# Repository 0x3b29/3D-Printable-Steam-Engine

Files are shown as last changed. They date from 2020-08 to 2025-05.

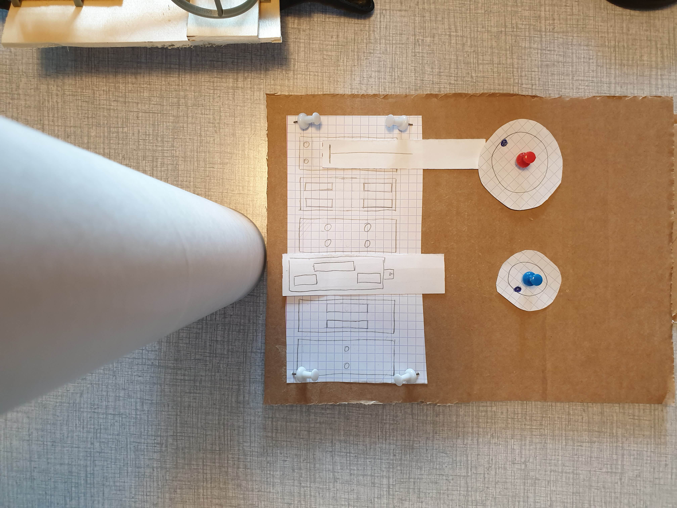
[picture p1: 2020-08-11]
Sketch/Step_2.jpg

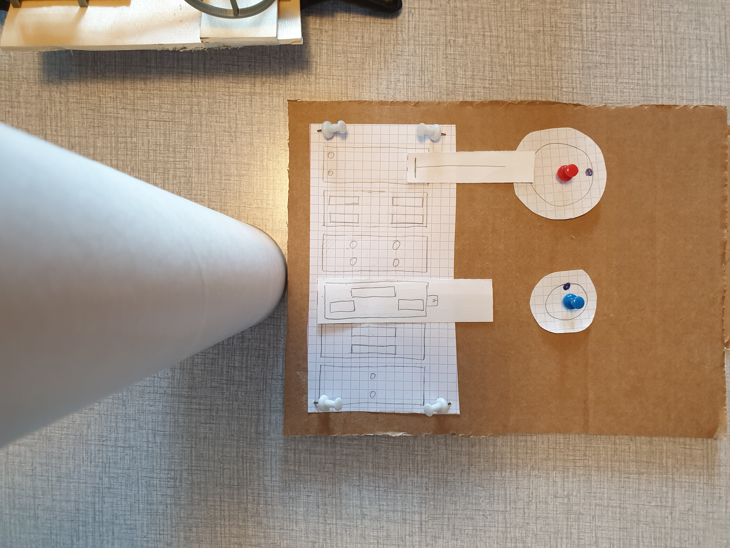
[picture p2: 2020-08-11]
Sketch/Step_5.jpg

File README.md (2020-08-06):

<h1>3D-Printable-Steam-Engine </h1>

<h2>Abstract</h2>

The goal of this project was to design a 3D printable steam engine. I challenged myself to come up with a design without looking up anything at all. I wanted to see how far I could get with only the knowledge I learned over time. To be honest, I did not expect getting very far, regardless getting a one and a four stroke variant to work.

<h2>Description</h2> 

This repository contains two variants of a design I came up in the spring 2020. It is inefficient and lacks the ability to work in both direktions. Also, there are quite some leeks which is an inherent flaw of 3D printing pressurized components whithout any seals. To get it to work, you need a source of pressurized gas. I used my dad's airbrush compressor. The air inlet in both designs is a replicaiton of the airbrush connection. This means you can connect a standard 2.5 mm hose to the 3D print. The 1 stroke design can operate with much lower pressure and spins at a higher rpm. The four stroke however is capable of starting in every position. The one stroke can stop at a dead point where you need to push it to get it spinning again. Also, since the leeks are four times higher in the four stroke engine, this variant uses much more air.

<h2>Printing</h2>
* All the parts can be printed in PLA (which I did). Since PLA is not very heat resilient, you should not try to power it with real steam tho
* Besides the crankshaft and the base, all other parts can be orientated in a way that they don't need supports
* All parts worked great printed with 0.2mm layer height
* To speed things up, the base plate and the stand can be printed whith 0.3mm layer height 

<h2>Assembly</h2>
* You need a 3mm drill to widen the holes in the lids. The pistons should slide smoothly through the cylinder and the lids. More clearance means less energy, so be conservative at first.
* You need a thin long strip op fine sanding paper to get the crankshafts smooth such that the connecting rods can move whithout a lot of resistance
* The Pistons need to be glued together. I used standard superglue for this. It is crucial that both piston halfs are very precisely glued to minimize friction
* You should break the corners of the slider(s) first to see if the sides need to be sanded down.
* To connect the piston rods with the pistons, I used small pieces of electrical copper wire.
* I did not need any oil to get both variants to work.

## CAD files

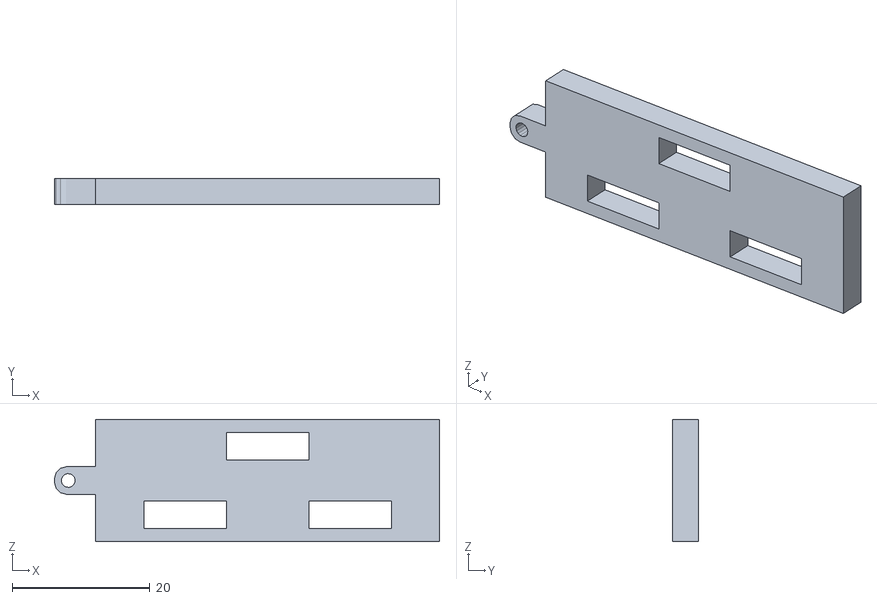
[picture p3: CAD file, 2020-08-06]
1 Stroke/Slider.stl
56.0 x 3.80 x 17.8

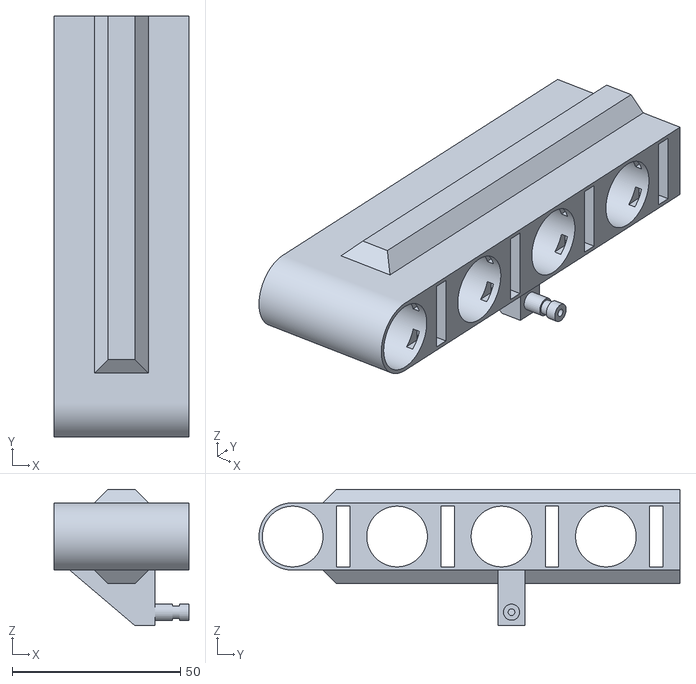
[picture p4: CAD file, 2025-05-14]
4 Stroke/Housing.stl
40.0 x 125.0 x 40.5

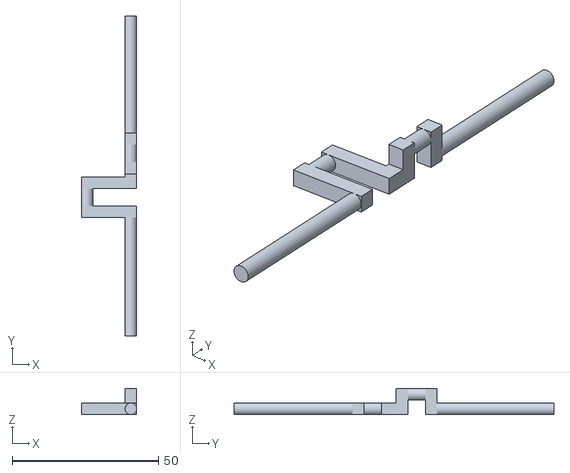
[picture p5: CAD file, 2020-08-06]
1 Stroke/Crank_Shaft.stl
19.0 x 109.5 x 9.00

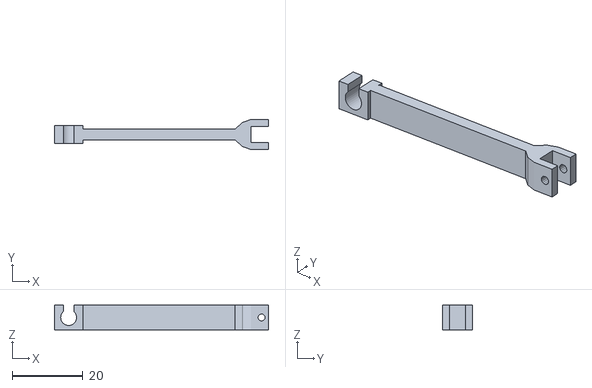
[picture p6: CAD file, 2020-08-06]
4 Stroke/Piston_Connecting_Rod.stl
60.5 x 8.50 x 7.00

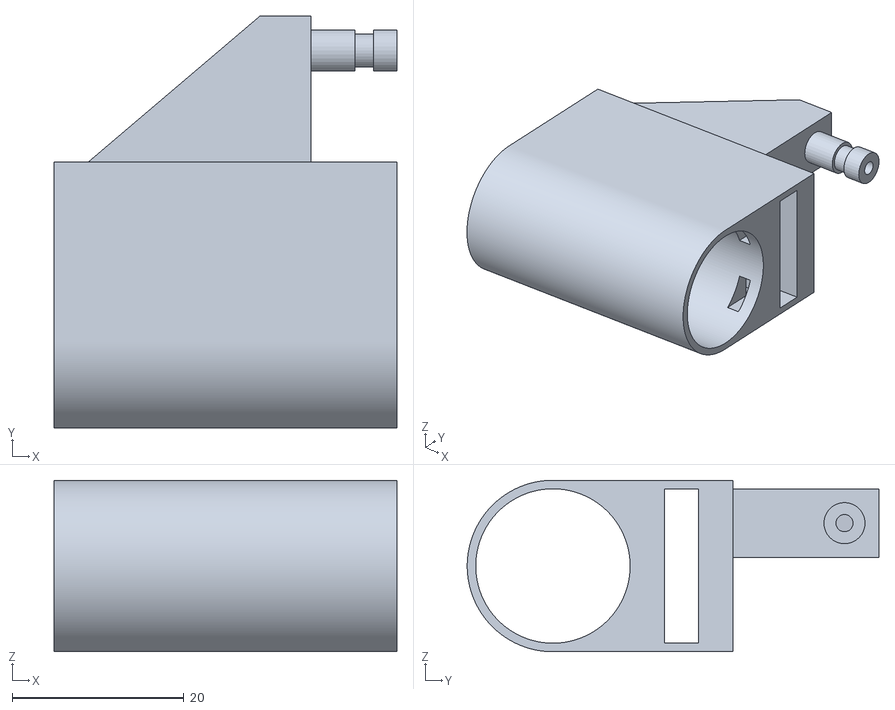
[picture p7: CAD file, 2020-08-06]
1 Stroke/Housing.stl
40.0 x 48.0 x 20.0

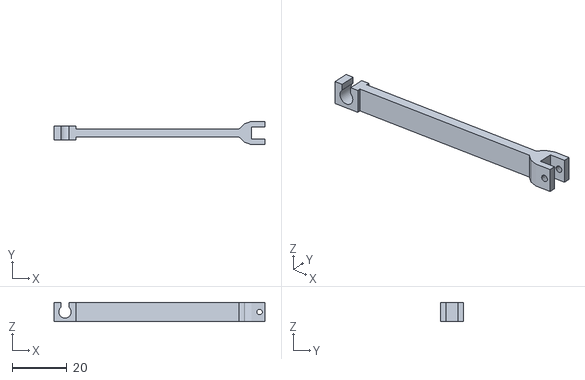
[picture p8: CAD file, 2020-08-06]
4 Stroke/Slider_Connecting_Rod.stl
77.0 x 8.50 x 7.01

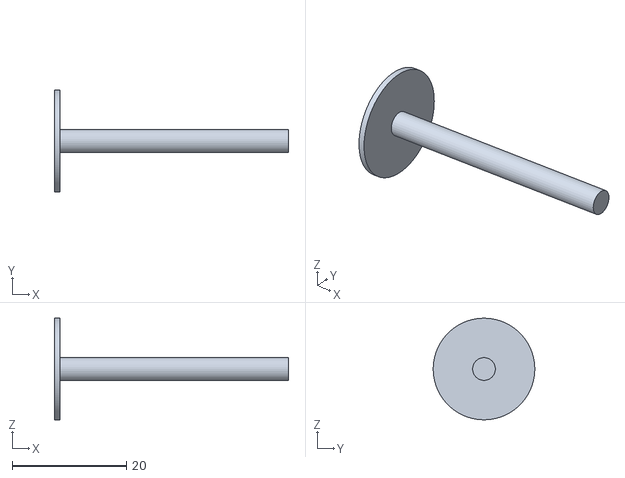
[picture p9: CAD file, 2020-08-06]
1 Stroke/Rear_Piston.stl
41.0 x 17.8 x 17.8

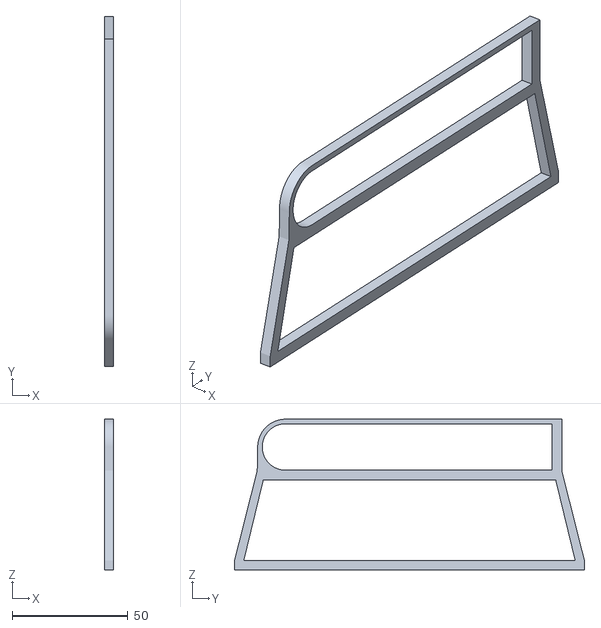
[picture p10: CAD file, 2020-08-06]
4 Stroke/Stand_Housing_Fixation_x2.stl
4.00 x 151.0 x 65.0

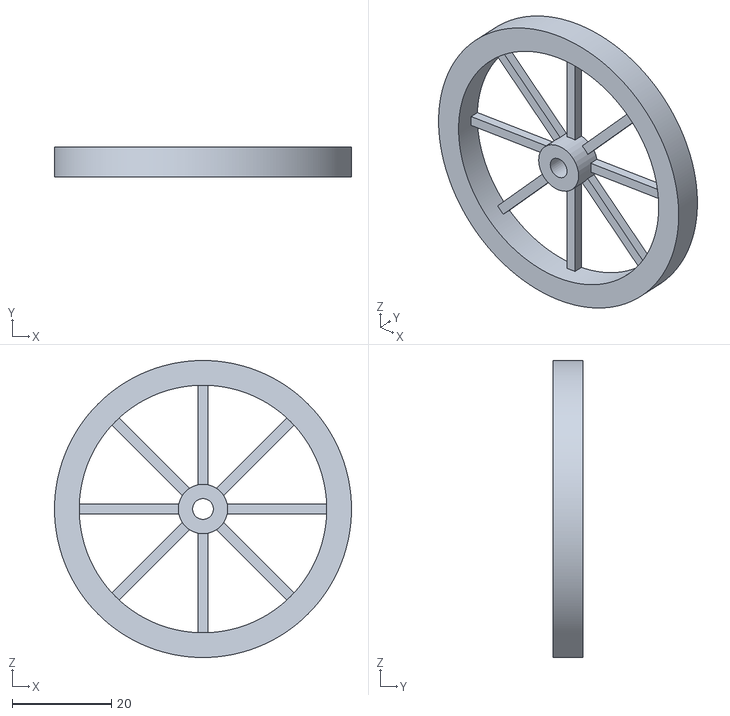
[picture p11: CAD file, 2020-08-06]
4 Stroke/Flywheel.stl
60.0 x 6.00 x 60.0

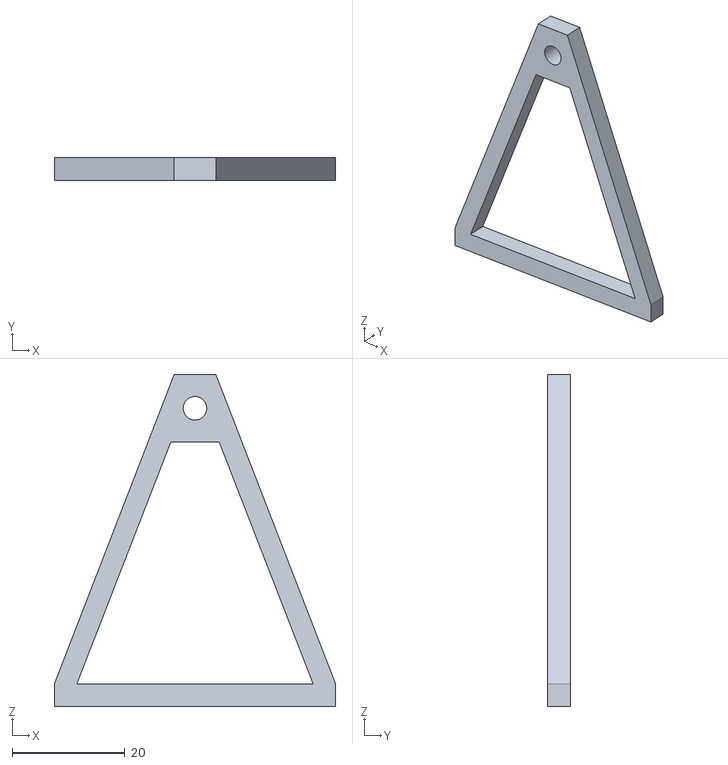
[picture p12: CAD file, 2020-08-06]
1 Stroke/Stand_Crankshaft_x2.stl
50.0 x 4.00 x 59.0

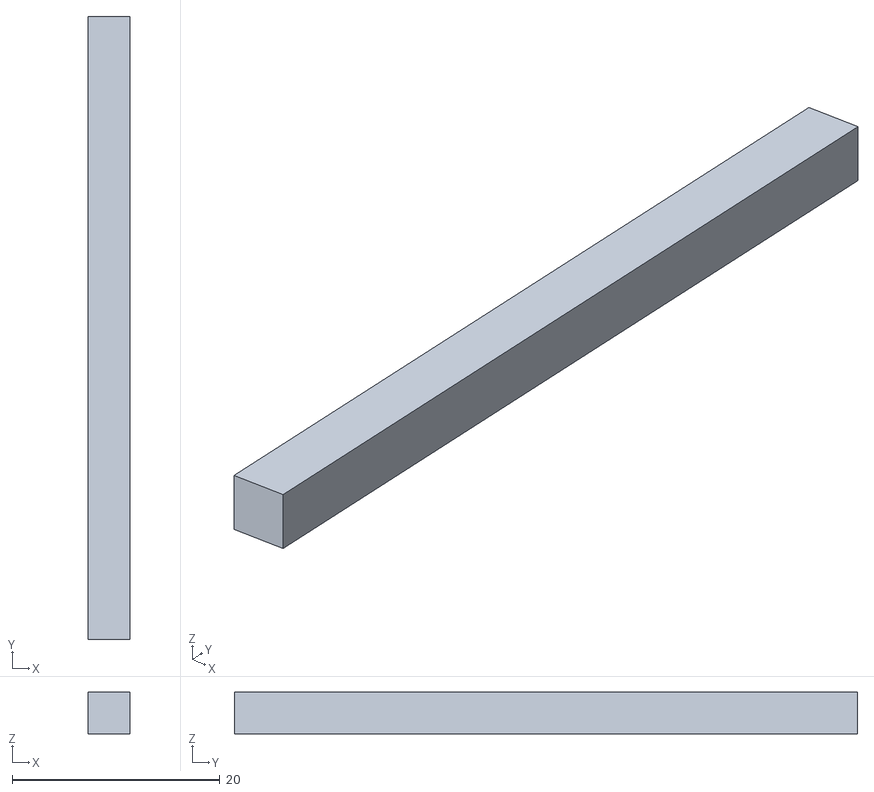
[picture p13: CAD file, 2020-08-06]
1 Stroke/Stand_Crankshaft_Fixation_x2.stl
4.00 x 60.0 x 4.00

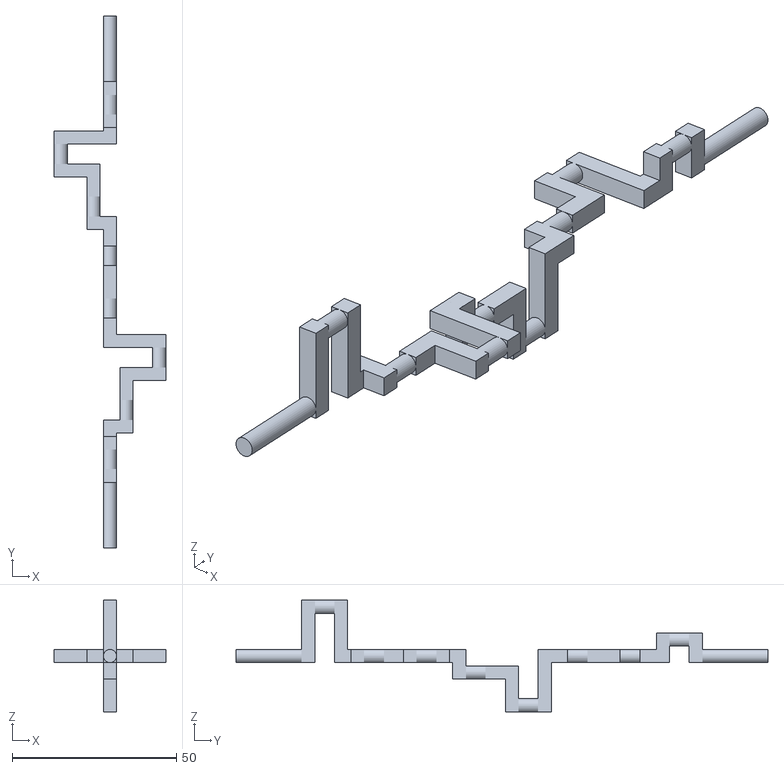
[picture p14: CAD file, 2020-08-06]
4 Stroke/Crankshaft.stl
34.0 x 162.0 x 34.0

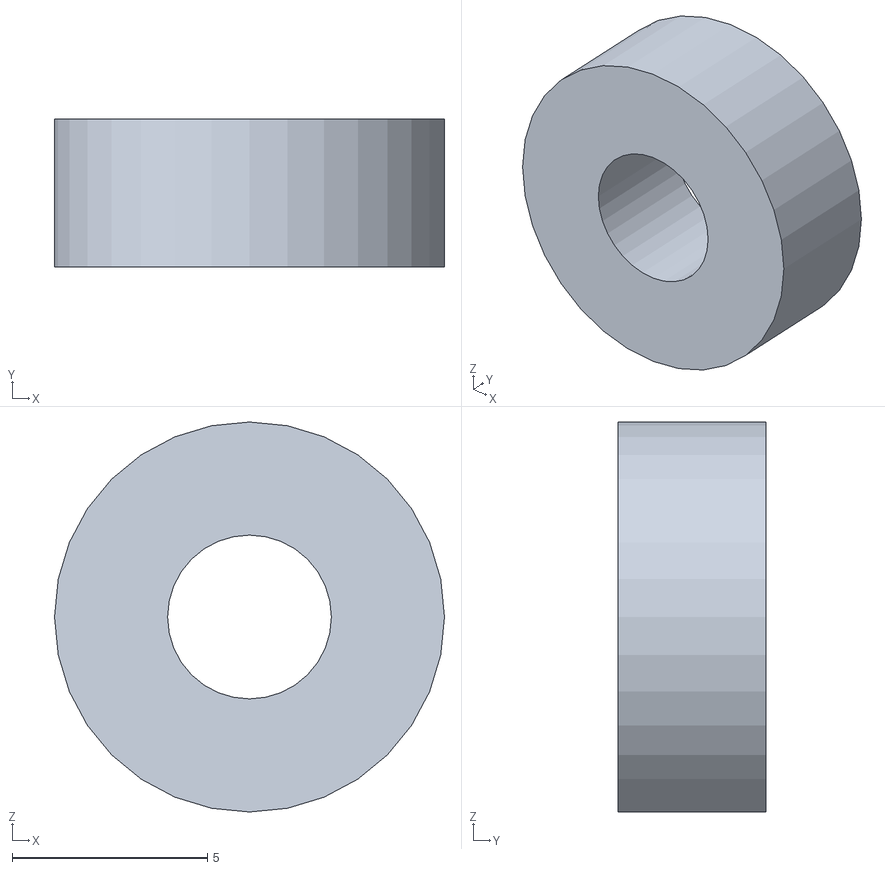
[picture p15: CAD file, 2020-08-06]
1 Stroke/Stopper_x2.stl
10.0 x 3.80 x 10.00

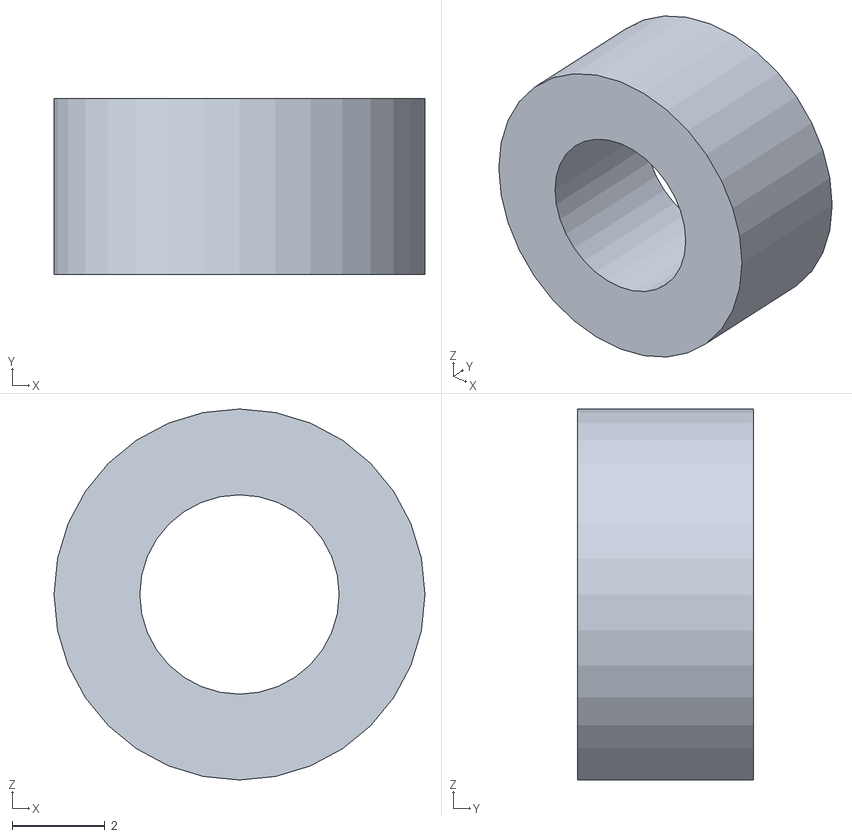
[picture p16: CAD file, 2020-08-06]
4 Stroke/Spacer_x4.stl
8.00 x 3.80 x 8.00

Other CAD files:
1 Stroke/Stand_Housing_Fixation_x2.stl
1 Stroke/Lid_x2.stl
1 Stroke/Piston_Front.stl
1 Stroke/Pulley.stl
1 Stroke/Stand.stl
1 Stroke/Stand_Housing_x2.stl
1 Stroke/steam_v1_0_1.blend
4 Stroke/Lid_x2.stl
4 Stroke/Piston_Front.stl
4 Stroke/Pulley.stl
4 Stroke/Stand.stl
4 Stroke/Stand_Housing_x2.stl

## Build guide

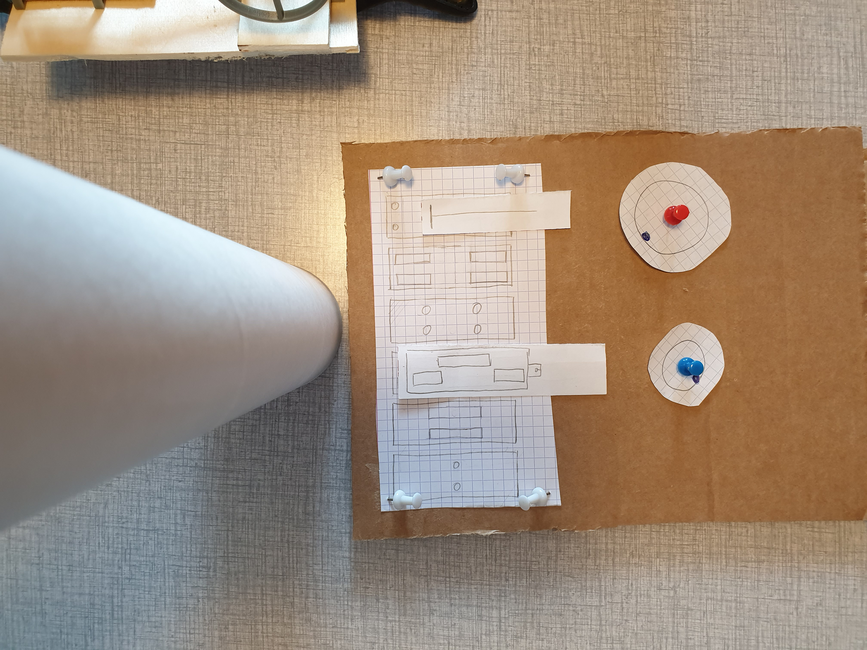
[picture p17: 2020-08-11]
Sketch/Step_8.jpg

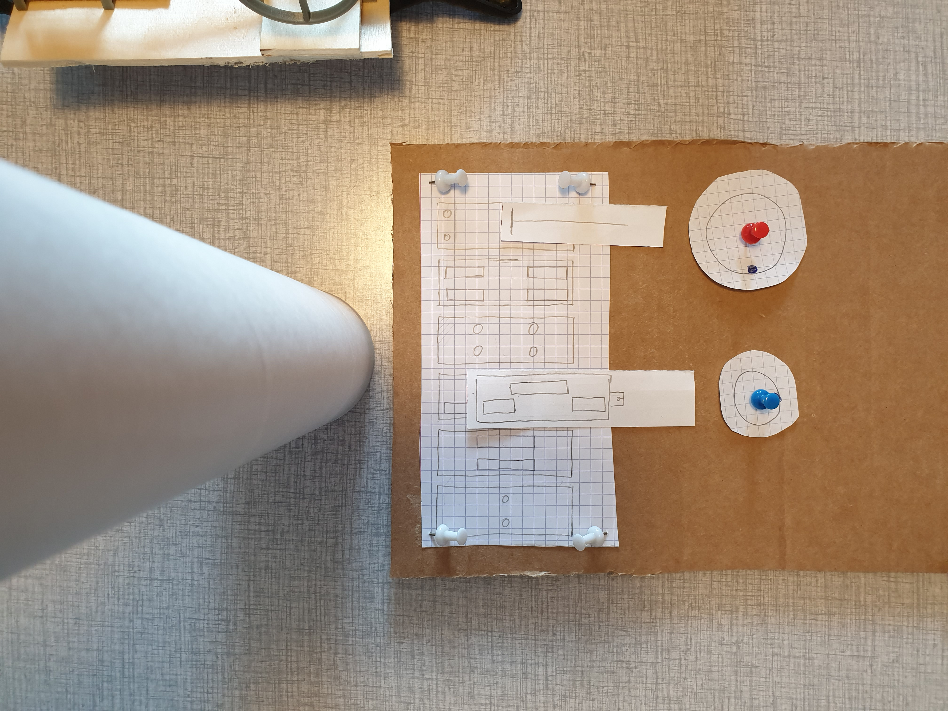
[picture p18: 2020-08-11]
Sketch/Step_7.jpg

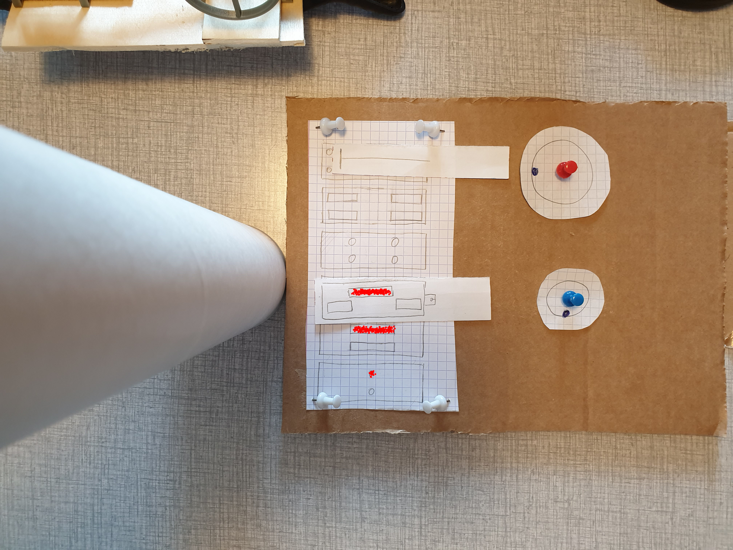
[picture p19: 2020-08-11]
Sketch/Step_1_Airflow.jpg

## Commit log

2020-08-06 inital save of my work to githu
    [Crank_Shaft.stl, Crankshaft.stl, Flywheel.stl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]
2020-08-11 assign materials to 1 stroke engine and create applied comonents
    [steam_v1_0_1.blend]
2020-08-11 assign materials to 4 stroke engine and create applied comonents
2025-05-14 add forgotten housing export to the 4 stroke engine stl's
    [Housing.stl]
